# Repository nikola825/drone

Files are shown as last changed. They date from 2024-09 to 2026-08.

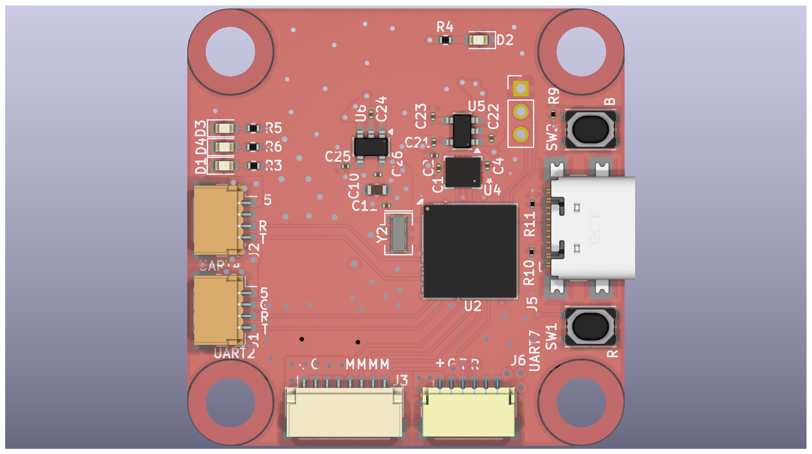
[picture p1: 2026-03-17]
hardware/fc/droneboardh723/render-top.png

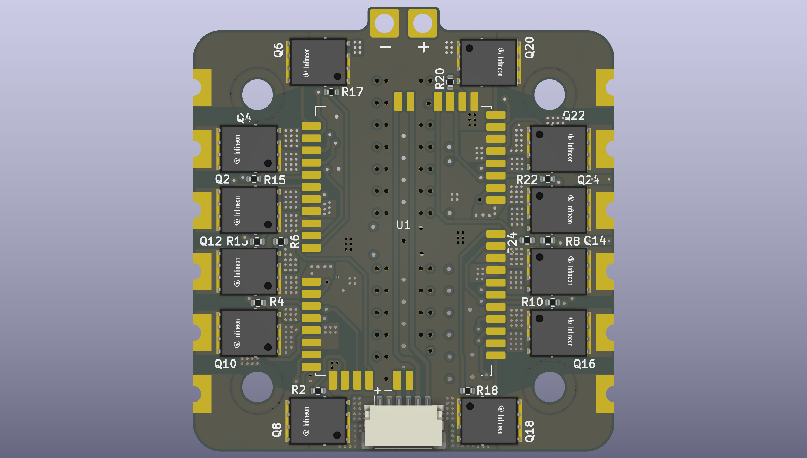
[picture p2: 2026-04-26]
hardware/esc/esc4x/power_board/top.png

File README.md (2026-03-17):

## 3D printable FPV quadcopter frame, SMT32-based flight controller and flight controller code

Hobby project, a homemade FPV drone with custom flight controller and frame.

### Current version - master branch
Folder contents (see readmes for more details):
- `3dp` - Freecad projects with 3D printable drone parts
- `code` - code for the flight controller
- `hardware` - KiCad projects for flight controller and esc PCB

Off the shelf parts you'll need:
- screws and screw related parts for the frame - see the readme in `3dp`
- motors and propellers
- ESC
- ELRS receiver
- Camera and VTX if you want FPV video

I couldn't be bothered to do in-detail docs, feel free to email me at (reverse the string to get my email) `moc.liamg@528alokin`

Do not use for anything serious, this was made by a man who started with zero knowledge of electronics, embedded development, rust development, flight controllers and 3D print design.
If you need something reliable, just get off-the-shelf stuff.

### Older versions
- `droneV1` branch contains the old Arduino-as-a-controller + MPU6050 version
- `droneV2` branch contains the old ATMEGA2560 flight controller board with an onboard MPU6050
- `droneV3` branch contains the work-in-progress version of the STM32F411 flight controller

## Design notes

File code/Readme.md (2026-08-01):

## Flight controller and configurator tool

This folder contains the flight_controller project to be flashed to the hardware in this repo.
It also contains the configurator GUI tool to configure motor mapping and directions of the flight controller.

### Contents
- `flight_controller` - Rust crate using the [Embassy](https://embassy.dev) implementing the flight control code
  - Cargo.toml contains feature flags for various variants of the FC PCB
  - Can be flashed through STM32 Cube programmer, dfu-util or probe-rs
- `configurator` - gui tool for configuring the motor mapping and directions
- `common` - stuff shared between configurator and FC
- `.vscode` and `.zed` - configurations for Rust analyzer for VSCode and Zed editors

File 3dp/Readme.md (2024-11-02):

## 3D printable 5-inch frame

- FcStd file contains the FreeCad project
- `complete.stl` - shows how the parts look assembled
- other STL files contain individual parts

Additional stuff needed for assembly:
- Screws - DIN 912 hex head screws of various lengths
  - M3x40 - 4 pieces
  - M3x12 - 8 pieces
  - M3x8 - 16 pieces
  - M3x20 - 4 pieces
- Heat set inserts M3, 4mm deep, 5mm wide - 8 pieces
- M3 5mm IN/OUT standoff - 8 pieces
- M3 30mm IN/IN standoffs - 8 pieces
- M3 washer - 8 pieces
- Silicone anti vibration mounts

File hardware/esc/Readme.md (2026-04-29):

# ESC

This folder contains PCBs for a 1x and a 4x ESC.
Mostly inspired by the [AM32 reference hardware](https://github.com/am32-firmware/am32-wiki/tree/ad24a0f2b645dd5e00588bb1a56035153b24e888/docs/development)

AM32REF_F051 target can be flashed using standard AM32 flashing process.

## esc1x
Contains one PCB for a single  ESC with solder points for power, control signal and ST-Link connections.

## esc4x 
Contains two PCBs - a logic board and a power board.

The boards are supposed to be soldered together using the castellated edges on the logic board and pads on the power board.

#### Logic board
This PCB contains the microcontrollers and gate drivers for the 4x esc.

It has no high power requirements. Can be fabricated as a cheaper 1 Oz/ft^2 thickness PCB

#### Power board
This PCB contains the mosfets, capacitors, regulators and connections for external stuff.

It is supposed to handle high currents of the motors and should be made with thicker 2 Oz/ft^2 copper.

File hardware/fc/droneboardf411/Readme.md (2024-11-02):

## Flight controller PCB
KiCad project and bom file for the flight controller PCB

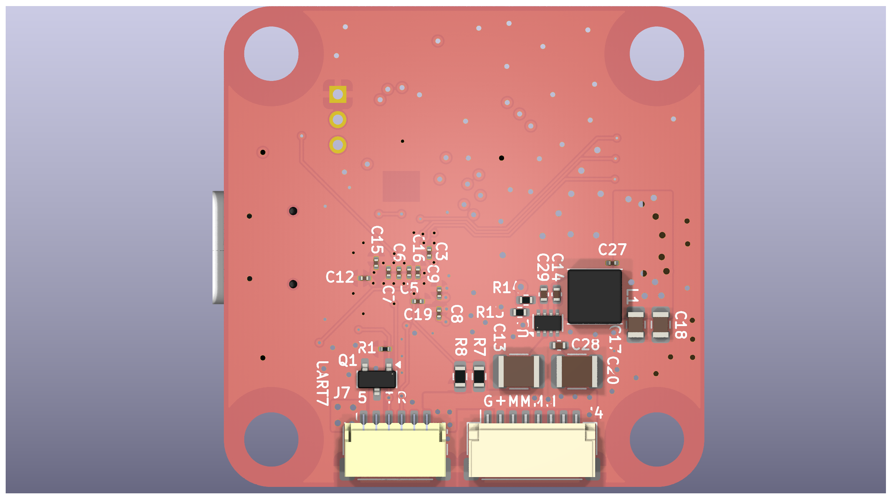
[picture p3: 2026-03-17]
hardware/fc/droneboardh723/render-bottom.png

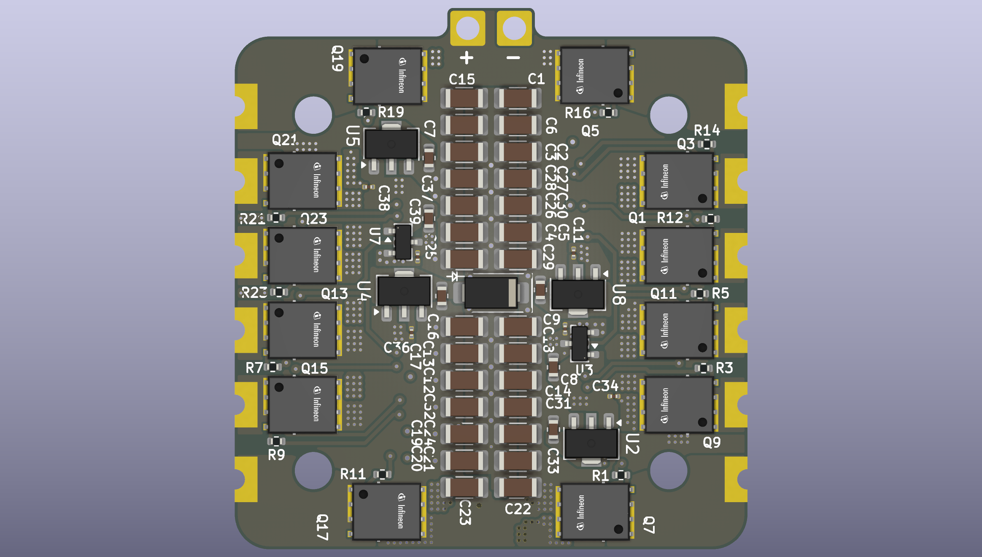
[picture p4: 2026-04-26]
hardware/esc/esc4x/power_board/bottom.png

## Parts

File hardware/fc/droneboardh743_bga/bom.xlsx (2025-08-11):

 |  |  | xxxx xxxx xxxxx xxPCS BOM (Sample Bill of Materials)
Item # | *Designator | *Qty | Manufacturer | *Mfg Part # | Description / Value | *Package/Footprint | Type | Your Instructions / Notes
1 | C3, C5, C6, C7, C8, C9, C16, C19, C27, C1 | 10 | Murata | GRM033R61A104KE15D | CAP CER 100nF 10V X5R 0201 | 0201 | SMD
2 | C12, C15, C2 | 3 | Murata | GRM033R61A225ME47D | CAP CER 2.2uF 10V X5R 0201 | 0201 | SMD
3 | C13, C20 | 2 | Samsung | CL32B106KBJNNNE | CAP CER 10uF 50V X7R 1210 | 1210 | SMD
4 | C14, C28 | 2 | Murata | GRM155R71H104KE14D | CAP CER 100nF 50V X7R 0402 | 0402 | SMD
5 | C17, C18 | 2 | Samsung | CL21A226MPQNNNE | CAP CER 22uF 10V X5R 0805 | 0805 | SMD
6 | C29 | 1 | Murata | GRM155R71H333KE14D | CAP CER 33nF 50V X7R 0402 | 0402 | SMD
7 | J4, J3 | 2 | JST | SM08B-SRSS-TB | JST SH Headers SMT SIDE 8-pin | JST SH 8-pin header | SMD
8 | J7, J6 | 2 | JST | SM06B-SRSS-TB | JST SH Headers SMT SIDE 6-pin | JST SH 6-pin header | SMD
9 | L1 | 1 | Coilcraft | XEL4030-332MEC | Power Inductors - SMD 3.3uH Shld 20% 6.6A 28.6mOhms AECQ2 | Inductor SMD 4x4mm | SMD
10 | Q1 | 1 | Diodes Incorporated | DMN3042L-7 | MOSFETs MOSFET N-CHANNEL 30V 5.8A SOT23-3 | SOT 23 | SMD
11 | R1, R9 | 2 | Yageo | RC0201FR-0710KL | RES 10K OHM 0.05W 1% 0201 | 0201 | SMD
12 | R7 | 1 | Yageo | RT0603BRD0710KL | RES 10K OHM 0.1W 0.1% 0603 | 0603 | SMD
13 | R8 | 1 | Yageo | RT0603BRD071KL | RES 1K OHM 0.1W 0.1% 0603 | 0603 | SMD
14 | R13, R3, R4, R5, R6 | 5 | Yageo | RC0402FR-071KL | RES 1K OHM 0.1W 1% 0402 | 0402 | SMD
15 | R14 | 1 | Yageo | RC0402FR-075K49L | RES 5.49K OHM 0.1W 1% 0402 | 0402 | SMD
16 | U1 | 1 | Texas Instruments | TPS62933FDRLR | Buck Switching Regulator IC Positive Adjustable 0.8V 1 Output 3A SOT-583 | SOT-583-8 | SMD
17 | C4, C23, C25 | 3 | Murata | GRM033R61C103KA12D | CAP CER 10nF 16V X5R 0201 | 0201 | SMD
18 | C10 | 1 | Samsung | CL10A106KP8NNNC | CAP CER 10uF 10V X5R 0603 | 0603 | SMD
19 | C11, C21, C22, C24, C26 | 5 | Murata | GRM033R61A105ME44D | CAP CER 1uF 10V X5R 0201 | 0201 | SMD
20 | D1 | 1 | Foshan NationStar | NCD0603Y5 | LED SMD Yellow 2V 20ma 0603 | 0603 | SMD
21 | D2 | 1 | Foshan NationStar | NCD0603R1 | LED SMD Red 2V 20ma 0603 | 0603 | SMD
22 | D3 | 1 | Foshan NationStar | NCD0603G3 | LED SMD Green 2V 20ma 0603 | 0603 | SMD
23 | D4 | 1 | Foshan NationStar | NCD0603B5 | LED SMD Blue 2V 20ma 0603 | 0603 | SMD
24 | J1, J2 | 2 | JST | SM04B-SRSS-TB | JST SH Headers SMT SIDE 4-pin | JST SH 4-pin header | SMD
25 | J5 | 1 | GCT | USB4110-GF-A | USB Connectors USB Type C, 2.0, Rec, SMT , G/F, RA , Top Mnt, T & R | USB-C | SMD
26 | R10, R11 | 2 | Yageo | RC0201FR-075K1L | RES 5.1K OHM 0.05W 1% 0201 | 0201 | SMD
27 | SW1, SW2 | 2 | Wurth Elektronik | 434133025816 | SWITCH TACTILE SPST-NO 0.05A 16V | Tactile switch 4.2x3.2mm | SMD
28 | U2 | 1 | STMicroelectronics | STM32H743VIH6 | ARM Microcontrollers - MCU High-performance, Arm Cortex-M7 MCU 2MBytes of Flash 1MB RAM | TFBGA-100 | SMD
29 | U4 | 1 | TDK Invensense | ICM-42688-P | IMUs - Inertial Measurement Units 6 Axis IMU Motion Tracking | LGA-14 3x2.5 P0.5 | SMD | Do not wash with ultrasound
30 | U5, U6 | 2 | MaxLinear | SPX3819M5-L-3-3/TR | LDO Voltage Regulators 500mA LOW NOISE LDO 3.3V | SOT-23-5 | SMD
31 | Y2 | 1 | Murata | CSTNE8M00G520000R0 | 8MHz 10pF SMD3213-3P Ceramic Resonators | 3-SMD, Non-Standard | SMD
Need a quick and accurante quote? Need an efficient production? Please read SMT Ordering Necessary Files & Info in 1 minute. Thank you very much! (https://www.pcbway.com/smt_ordering_guide.html)
Click for Instructions on How to Create a BOM (https://www.pcbway.com/blog/PCB_Assembly/How_to_Build_a_BOM__Bill_Of_Materials_.html)

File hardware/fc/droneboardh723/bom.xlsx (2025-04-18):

 |  |  | xxxx xxxx xxxxx xxPCS BOM (Sample Bill of Materials)
Item # | *Designator | *Qty | Manufacturer | *Mfg Part # | Description / Value | *Package/Footprint | Type | Your Instructions / Notes
1 | C13 | 1 | Don’t care | Don’t care | CAP CER 10uF 25V X7R 1210 | 1210 | SMD | Don’t care about model/manufacturer, just make sure it fits description
2 | C14 | 1 | Don’t care | Don’t care | CAP CER 100nF 25V X7R 0603 | 0603 | SMD | Don’t care about model/manufacturer, just make sure it fits description
3 | C17, C18 | 2 | Don’t care | Don’t care | CAP CER 22uF 10V X5R 0805 | 0805 | SMD | Don’t care about model/manufacturer, just make sure it fits description
4 | C1, C3, C5, C6, C7, C8, C9, C16 | 8 | Don’t care | Don’t care | CAP CER 100nF 16V X5R 0201 | 0201 | SMD | Don’t care about model/manufacturer, just make sure it fits description
5 | C2, C12, C15 | 3 | Don’t care | Don’t care | CAP CER 2.2uF 10V X5R 0201 | 0201 | SMD | Don’t care about model/manufacturer, just make sure it fits description
6 | C4, C23, C25 | 3 | Don’t care | Don’t care | CAP CER 10nF 16V X5R 0201 | 0201 | SMD | Don’t care about model/manufacturer, just make sure it fits description
7 | C10 | 1 | Don’t care | Don’t care | CAP CER 10uF 10V X5R 0402 | 0402 | SMD | Don’t care about model/manufacturer, just make sure it fits description
8 | C11, C21, C22, C24, C26 | 5 | Don’t care | Don’t care | CAP CER 1uF 10V X5R 0201 | 0201 | SMD
9 | D1 | 1 | Foshan NationStar | NCD0603Y5 | LED SMD Yellow 2V 20ma 0603 | 0603 | SMD
10 | D2 | 1 | Foshan NationStar | NCD0603R1 | LED SMD Red 2V 20ma 0603 | 0603 | SMD
11 | D3 | 1 | Foshan NationStar | NCD0603G3 | LED SMD Green 2V 20ma 0603 | 0603 | SMD
12 | D4 | 1 | Foshan NationStar | NCD0603B5 | LED SMD Blue 2V 20ma 0603 | 0603 | SMD
13 | J5 | 1 | GCT | USB4110-GF-A | USB Connectors USB Type C, 2.0, Rec, SMT , G/F, RA , Top Mnt, T & R | USB-C | SMD
14 | R1, R2, R9, R12 | 4 | Don’t care | Don’t care | RES 10K OHM 0.05W 1% 0201 | 0201 | SMD | Don’t care about model/manufacturer, just make sure it fits description
15 | R14 | 1 | Don’t care | Don’t care | RES 5.49K OHM 0.1W 1% 0402 | 0402 | SMD | Don’t care about model/manufacturer, just make sure it fits description
16 | R3, R4, R5, R6, R13 | 5 | Don’t care | Don’t care | RES 1K OHM 0.1W 1% 0402 | 0402 | SMD | Don’t care about model/manufacturer, just make sure it fits description
17 | R8 | 1 | Don’t care | Don’t care | RES 1K OHM 0.1W 0.1% 0603 | 0603 | SMD | Don’t care about model/manufacturer, just make sure it fits description
18 | R7 | 1 | Don’t care | Don’t care | RES 10K OHM 0.1W 0.1% 0603 | 0603 | SMD | Don’t care about model/manufacturer, just make sure it fits description
19 | R10, R11 | 2 | Don’t care | Don’t care | RES 5.1K OHM 0.05W 1% 0201 | 0201 | SMD | Don’t care about model/manufacturer, just make sure it fits description
20 | U1 | 1 | Diodes Incorporated | AP62300Z6-7 | Switching Voltage Regulators DCDC Conv HV Buck SOT563(STD) T&R 3K | SOT 563 | SMD
21 | U2 | 1 | STMicroelectronics | STM32H723VGT6 | ARM Microcontrollers High-performance, Arm Cortex-M7 MCU 1 MByte Flash, 564 Kbytes RAM | LQFP-100 | SMD
22 | U4 | 1 | TDK Invensense | ICM-42688-P | IMUs - Inertial Measurement Units 6 Axis IMU Motion Tracking | LGA-14 3x2.5 P0.5 | SMD | Do not wash with ultrasound
23 | U5, U6 | 2 | MaxLinear | SPX3819M5-L-3-3/TR | LDO Voltage Regulators 500mA LOW NOISE LDO 3.3V | SOT-23-5 | SMD
24 | Y2 | 1 | Murata Electronics | CSTNE20M0V53Z000R0 | Resonators 20.0 MHZ 15PF | 3-SMD, Non-Standard | SMD
25 | L1 | 1 | Coilcraft | XEL4030-332MEC | Power Inductors - SMD 3.3uH Shld 20% 6.6A 28.6mOhms AECQ2 | Inductor SMD 4x4mm | SMD
Need a quick and accurante quote? Need an efficient production? Please read SMT Ordering Necessary Files & Info in 1 minute. Thank you very much! (https://www.pcbway.com/smt_ordering_guide.html)
Click for Instructions on How to Create a BOM (https://www.pcbway.com/blog/PCB_Assembly/How_to_Build_a_BOM__Bill_Of_Materials_.html)

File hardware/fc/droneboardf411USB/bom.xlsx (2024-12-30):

 |  |  | xxxx xxxx xxxxx xxPCS BOM (Sample Bill of Materials)
Item # | *Designator | *Qty | Manufacturer | *Mfg Part # | Description / Value | *Package/Footprint | Type | Your Instructions / Notes
1 | C4, C23, C25 | 3 | Don’t care | Don’t care | CAP CER 10nF 16V X7R 0603 | 0603 | SMD | Don’t care about model/manufacturer, just make sure it fits description
2 | C1, C20 | 2 | Don’t care | Don’t care | CAP CER 100nF 16V X7R 0603 | 0603 | SMD | Don’t care about model/manufacturer, just make sure it fits description
3 | C3, C5, C6, C7, C9, C16 | 6 | Don’t care | Don’t care | CAP CER 100nF 16V X7R 0402 | 0402 | SMD | Don’t care about model/manufacturer, just make sure it fits description
4 | C19 | 1 | Don’t care | Don’t care | CAP CER 330nF 25V X7R 0805 | 0805 | SMD | Don’t care about model/manufacturer, just make sure it fits description
5 | C11, C21, C22, C24, C26 | 5 | Don’t care | Don’t care | CAP CER 1uF 16V X5R 0805 | 0805 | SMD | Don’t care about model/manufacturer, just make sure it fits description
6 | C2 | 1 | Don’t care | Don’t care | CAP CER 2.2uF 16V X7R 0805 | 0805 | SMD | Don’t care about model/manufacturer, just make sure it fits description
7 | C15 | 1 | Don’t care | Don’t care | CAP CER 4.7uF 16V X7R 1206 | 1206 | SMD | Don’t care about model/manufacturer, just make sure it fits description
8 | C10 | 1 | Don’t care | Don’t care | CAP CER 10uF 16V X7R 1206 | 1206 | SMD | Don’t care about model/manufacturer, just make sure it fits description
9 | D1 | 1 | Foshan NationStar | NCD0603Y5 | LED SMD Yellow 2V 20ma 0603 | 0603 | SMD
10 | D2 | 1 | Foshan NationStar | NCD0603R1 | LED SMD Red 2V 20ma 0603 | 0603 | SMD
11 | D3 | 1 | Foshan NationStar | NCD0603G3 | LED SMD Green 2V 20ma 0603 | 0603 | SMD
12 | D4 | 1 | Foshan NationStar | NCD0603B5 | LED SMD Blue 2V 20ma 0603 | 0603 | SMD
13 | R1,R2,R9 | 3 | Don’t care | Don’t care | RES 10K OHM 0.1W 1% 0402 SMD | 0402 | SMD | Don’t care about model/manufacturer, just make sure it fits description
14 | R7 | 1 | Don’t care | Don’t care | RES 10K OHM 0.1W 0.1% 0603 SMD | 0603 | SMD | Don’t care about model/manufacturer, just make sure it fits description
15 | R3, R4, R5, R6 | 4 | Don’t care | Don’t care | RES 1K OHM 0.1W 1% 0402 SMD | 0402 | SMD | Don’t care about model/manufacturer, just make sure it fits description
16 | R8 | 1 | Don’t care | Don’t care | RES 1K OHM 0.1W 0.1% 0603 SMD | 0603 | SMD | Don’t care about model/manufacturer, just make sure it fits description
17 | U1 | 1 | STMicroelectronics | STM32F411CEU6 | ARM Microcontrollers - MCU High-performance access line, Arm Cortex-M4 core DSP & FPU, 512 Kbytes of Flash | QFN-48 | SMD
18 | U3 | 1 | STMicroelectronics | L78M05CDT | Linear Voltage Regulators 5.0V 0.5A Positive | TO-252-2 | SMD
19 | U4 | 1 | TDK Invensense | ICM-42688-P | IMUs - Inertial Measurement Units 6 Axis IMU Motion Tracking | LGA-14 3x2.5 P0.5 | SMD
20 | U5,U6 | 2 | STMicroelectronics | LDK130M33R | LDO Voltage Regulators 300mA low Q LDO 1.9 to 5.5V 100mV | SOT-23-5 | SMD
21 | Y2 | 1 | Murata Electronics | CSTNE20M0V53Z000R0 | Resonators 20.0 MHZ 15PF | 3-SMD, Non-Standard | SMD
22 | J2 | 1 | Molex | 47346-0001 | USB Connectors MICRO USB B RECPT BTTM MOUNT | SMD | SMD
Need a quick and accurante quote? Need an efficient production? Please read SMT Ordering Necessary Files & Info in 1 minute. Thank you very much! (https://www.pcbway.com/smt_ordering_guide.html)
Click for Instructions on How to Create a BOM (https://www.pcbway.com/blog/PCB_Assembly/How_to_Build_a_BOM__Bill_Of_Materials_.html)

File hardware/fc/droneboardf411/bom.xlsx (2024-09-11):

 |  |  | xxxx xxxx xxxxx xxPCS BOM (Sample Bill of Materials)
Item # | *Designator | *Qty | Manufacturer | *Mfg Part # | Description / Value | *Package/Footprint | Type | Your Instructions / Notes
1 | C4, C23, C25 | 3 | Don’t care | Don’t care | CAP CER 10nF 16V X7R 0603 | 0603 | SMD | Don’t care about model/manufacturer, just make sure it fits description
2 | C1, C20 | 2 | Don’t care | Don’t care | CAP CER 100nF 16V X7R 0603 | 0603 | SMD | Don’t care about model/manufacturer, just make sure it fits description
3 | C3, C5, C6, C7, C9, C16 | 6 | Don’t care | Don’t care | CAP CER 100nF 16V X7R 0402 | 0402 | SMD | Don’t care about model/manufacturer, just make sure it fits description
4 | C19 | 1 | Don’t care | Don’t care | CAP CER 330nF 25V X7R 0805 | 0805 | SMD | Don’t care about model/manufacturer, just make sure it fits description
5 | C11, C21, C22, C24, C26 | 5 | Don’t care | Don’t care | CAP CER 1uF 16V X5R 0805 | 0805 | SMD | Don’t care about model/manufacturer, just make sure it fits description
6 | C2 | 1 | Don’t care | Don’t care | CAP CER 2.2uF 16V X7R 0805 | 0805 | SMD | Don’t care about model/manufacturer, just make sure it fits description
 | C15 | 1 | Don’t care | Don’t care | CAP CER 4.7uF 16V X7R 1206 | 1206 | SMD | Don’t care about model/manufacturer, just make sure it fits description
 | C10 | 1 | Don’t care | Don’t care | CAP CER 10uF 16V X7R 1206 | 1206 | SMD | Don’t care about model/manufacturer, just make sure it fits description
 | D1 | 1 | Don’t care | Don’t care | LED SMD Yellow 2V 20ma 0603 | 0603 | SMD | Don’t care about model/manufacturer, just make sure it fits description
 | D2 | 1 | Don’t care | Don’t care | LED SMD Red 2V 20ma 0603 | 0603 | SMD | Don’t care about model/manufacturer, just make sure it fits description
 | D3 | 1 | Don’t care | Don’t care | LED SMD Green 2V 20ma 0603 | 0603 | SMD | Don’t care about model/manufacturer, just make sure it fits description
 | D4 | 1 | Don’t care | Don’t care | LED SMD Blue 2V 20ma 0603 | 0603 | SMD | Don’t care about model/manufacturer, just make sure it fits description
 | R1,R2,R9 | 3 | Don’t care | Don’t care | RES 10K OHM 0.1W 1% 0402 SMD | 0402 | SMD | Don’t care about model/manufacturer, just make sure it fits description
 | R7 | 1 | Don’t care | Don’t care | RES 10K OHM 0.1W 1% 0603 SMD | 0603 | SMD | Don’t care about model/manufacturer, just make sure it fits description
 | R3, R4, R5, R6 | 4 | Don’t care | Don’t care | RES 1K OHM 0.1W 1% 0402 SMD | 0402 | SMD | Don’t care about model/manufacturer, just make sure it fits description
 | R8 | 1 | Don’t care | Don’t care | RES 1K OHM 0.1W 1% 0603 SMD | 0603 | SMD | Don’t care about model/manufacturer, just make sure it fits description
 | U1 | 1 | STMicroelectronics | STM32F411CEU6 | ARM Microcontrollers - MCU High-performance access line, Arm Cortex-M4 core DSP & FPU, 512 Kbytes of Flash | QFN-48 | SMD
 | U3 | 1 | STMicroelectronics | L78M05CDT | Linear Voltage Regulators 5.0V 0.5A Positive | TO-252-2 | SMD
 | U4 | 1 | TDK Invensense | ICM-42688-P | IMUs - Inertial Measurement Units 6 Axis IMU Motion Tracking | LGA-14 3x2.5 P0.5 | SMD
 | U5,U6 | 2 | STMicroelectronics | LDK130M33R | LDO Voltage Regulators 300mA low Q LDO 1.9 to 5.5V 100mV | SOT-23-5 | SMD
 | Y2 | 1 | Murata Electronics | CSTNE20M0V53Z000R0 | Resonators 20.0 MHZ 15PF | 3-SMD, Non-Standard | SMD
Need a quick and accurante quote? Need an efficient production? Please read SMT Ordering Necessary Files & Info in 1 minute. Thank you very much! (https://www.pcbway.com/smt_ordering_guide.html)
Click for Instructions on How to Create a BOM (https://www.pcbway.com/blog/PCB_Assembly/How_to_Build_a_BOM__Bill_Of_Materials_.html)

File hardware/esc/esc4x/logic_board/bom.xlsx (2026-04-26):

 |  |  | xxxx xxxx xxxxx xxPCS BOM (Sample Bill of Materials)
Item # | *Designator | *Qty | Manufacturer | *Mfg Part # | Description / Value | *Package/Footprint | Type | Your Instructions / Notes
1 | R5,R39,R8,R3,R23,R18,R24,R37,R42,R27,R11,R26,R36,R20,R15,R9,R30,R13,R16,R6,R1,R44,R40,R34,R29,R22,R32,R12 | 28 | Yageo | RC0201FR-0710KL | RES 10K OHM 0.05W 1% 0201 | 0201 | SMD
2 | R38,R31,R41,R17,R14,R4,R7,R10,R2,R21,R25,R43,R28,R35,R33,R19 | 16 | Yageo | RC0201FR-071KL | RES 1K OHM 0.05W 1% 0201 | 0201 | SMD
3 | U3,U1,U7,U5 | 4 | STMicroelectronics | STM32F051K8U6TR | ARM Microcontrollers - MCU ARM Cortex-M0 MCU 64Kb Flash 48MHz | UFQFPN-32 | SMD
4 | C23,C5,C33,C9,C10,C18,C27,C32,C22,C31,C42,C43,C38,C11,C24,C44 | 16 | Murata | GRM033R61A105ME44D | CAP CER 1uF 10V X5R 0201 | 0201 | SMD
5 | C21,C2,C12,C3,C8,C35,C36,C1,C30,C14,C13,C17,C25,C15,C34,C41 | 16 | Murata | GRM033R61A104KE15D | CAP CER 100nF 10V X5R 0201 | 0201 | SMD
6 | C4,C7,C26,C40,C29,C37,C20,C16 | 8 | Samsung | CL05A106MP5NUNC | CAP CER 10uF 10V X5R 0402 | 0402 | SMD
7 | C19,C6,C39,C28 | 4 | Murata | GRM033R61C103KA12D | CAP CER 10nF 16V X5R 0201 | 0201 | SMD
8 | U6,U8,U2,U4 | 4 | Texas instruments | DRV8300DRGER | Gate Drivers 100-V max simple 3-p hase gate driver | VQFN-24 | SMD
Need a quick and accurante quote? Need an efficient production? Please read SMT Ordering Necessary Files & Info in 1 minute. Thank you very much! (https://www.pcbway.com/smt_ordering_guide.html)
Click for Instructions on How to Create a BOM (https://www.pcbway.com/blog/PCB_Assembly/How_to_Build_a_BOM__Bill_Of_Materials_.html)

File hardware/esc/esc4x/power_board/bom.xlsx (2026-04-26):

 |  |  | xxxx xxxx xxxxx xxPCS BOM (Sample Bill of Materials)
Item # | *Designator | *Qty | Manufacturer | *Mfg Part # | Description / Value | *Package/Footprint | Type | Your Instructions / Notes
1 | C1, C2, C3, C4, C5, C6, C7, C12, C13, C14, C15, C16, C17, C18, C19, C20, C21, C22, C23, C24, C25, C26, C27, C28, C29, C30, C31, C32 | 28 | TDK | C3216X5R1E476M160AC | CAP CER 47uF 25V X5R 1206 | 1206 | SMD
2 | C8, C10, C33, C35, C37, C39 | 6 | Murata | GCJ188R71E105KA01D | CAP CER 1uF 25V X7R 0603 | 0603 | SMD
3 | C9, C11, C34, C36, C38, C40 | 6 | Murata | GRM033R61A105ME44D | CAP CER 1uF 10V X5R 0201 | 0201 | SMD
4 | D3 | 1 | Yageo | SMAJ26A-HP6AT | VS Diodes SMAJ DO214AC 26V 42.1V AEC-Q101 | DO-214AC | SMD
5 | J1 | 1 | JST | SM06B-SRSS-TB | JST SH Headers SMT SIDE 6-pin | JST SH 6-pin header | SMD
6 | Q1, Q2, Q3, Q4, Q5, Q6, Q7, Q8, Q9, Q10, Q11, Q12, Q13, Q14, Q15, Q16, Q17, Q18, Q19, Q20, Q21, Q22, Q23, Q24 | 24 | Infineon | BSC010N04LS6 | N-Channel 40 V 100A 3W Surface Mount PG-TDSON-8-6 | TDSON-8-FL | SMD
7 | R1, R2, R3, R4, R5, R6, R7, R8, R9, R10, R11, R12, R13, R14, R15, R16, R17, R18, R19, R20, R21, R22, R23, R24 | 24 | Yageo | RC0402FR-0720RL | RES 20 OHM 0.067W 1% 0402 | 0402 | SMD
8 | U2, U4, U5, U8 | 4 | Diodes incorporated | AP7381-50Y-13 | LDO Voltage Regulators 150mA 5V | SOT-89-3 | SMD
9 | U3, U7 | 2 | Diodes incorporated | AP7381-33SA-7 | LDO Voltage Regulator 100mA 3.3V | SOT-23-3 | SMD
Need a quick and accurante quote? Need an efficient production? Please read SMT Ordering Necessary Files & Info in 1 minute. Thank you very much! (https://www.pcbway.com/smt_ordering_guide.html)
Click for Instructions on How to Create a BOM (https://www.pcbway.com/blog/PCB_Assembly/How_to_Build_a_BOM__Bill_Of_Materials_.html)

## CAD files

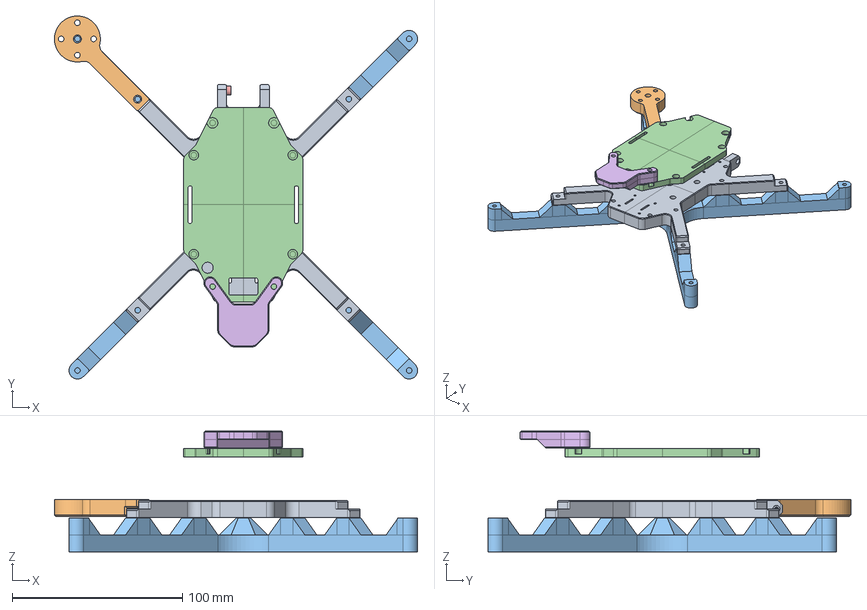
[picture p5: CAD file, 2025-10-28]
3dp/seven_inch/whole_assembly.step
213.1 x 213.0 x 70.9 mm
Center
Arm
Legs
Top
CameraAttachment
GPSPlate

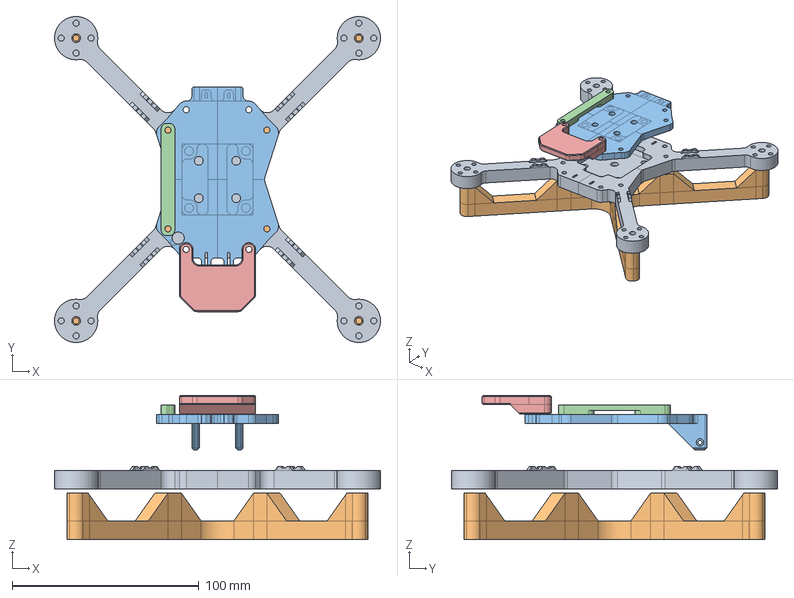
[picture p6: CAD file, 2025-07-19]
3dp/five_inch/whole_assembly.step
174.5 x 174.5 x 77.3 mm
Bottom
Legs
Top
TiePoint
GPSPlate

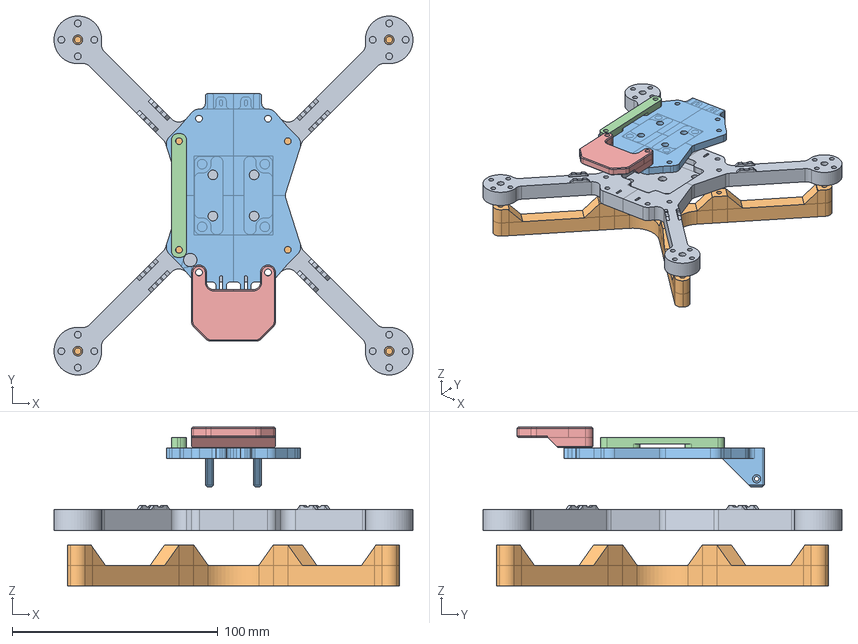
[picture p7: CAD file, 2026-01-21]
3dp/five_inch/five_inch.FCStd
174.5 x 174.5 x 77.3 mm
Bottom
Legs
Top
TiePoint
GPSPlate

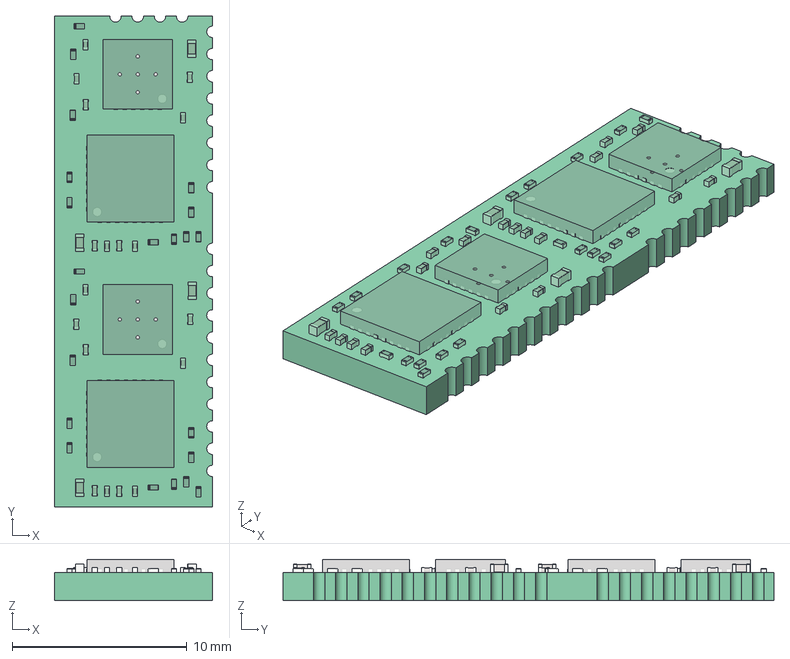
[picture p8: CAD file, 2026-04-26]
hardware/esc/esc4x/logic_board/logic_board1-logic_board.step
9.04 x 28.1 x 2.37 mm
Pcb_7dd1
R5_R_0201_0603Metric_fb9afff6527c x 22
U3_QFN-32-1EP_5x5mm_Pitch0.5mm_a1086153c562 x 2
C23_C_0201_0603Metric_5a5157595c69 x 18
C4_C_0402_1005Metric_eb0286e01f0b x 4
U2_QFN-24-1EP_4x4mm_Pitch0.5mm_a600a1f0b4fe[2] x 2

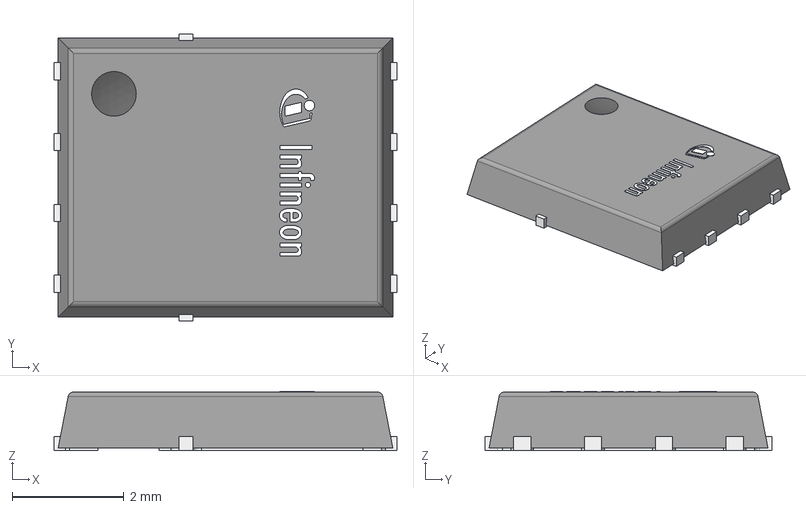
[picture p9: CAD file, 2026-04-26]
hardware/esc/esc4x/power_board/components/3dmodels/PG_TDSON_FL.stp
6.15 x 5.15 x 1.06 mm

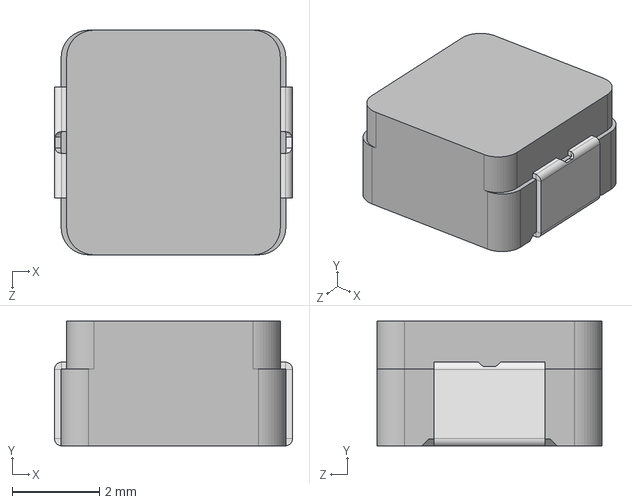
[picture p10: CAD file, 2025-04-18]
hardware/fc/droneboardh723/components/3dmodels/IHLP2020CZ.STEP
5.45 x 2.86 x 5.15 mm

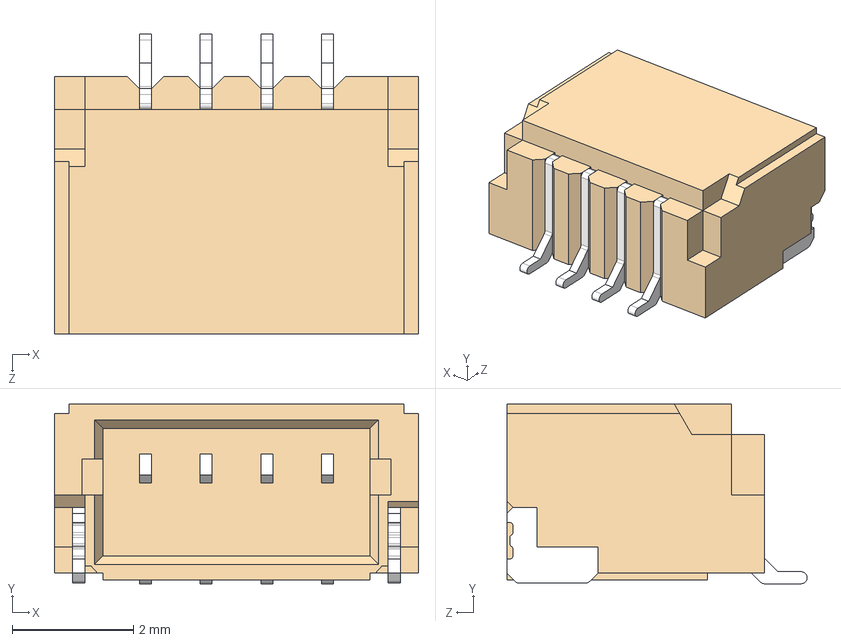
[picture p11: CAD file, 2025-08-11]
hardware/fc/droneboardh743_bga/components/3dmodels/SM04B-SRSS-TB_LF__SN_.stp
6.00 x 2.96 x 4.95 mm

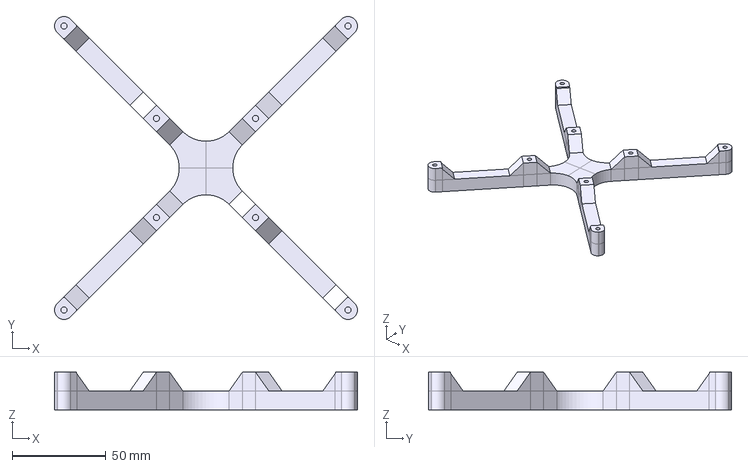
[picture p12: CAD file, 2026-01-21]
3dp/five_inch/legs.step
161.4 x 161.4 x 20.0 mm

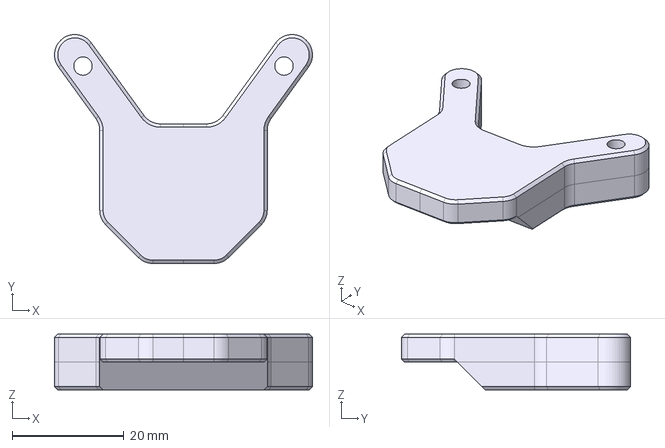
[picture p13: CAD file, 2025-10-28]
3dp/seven_inch/gps_plate.step
46.2 x 41.0 x 10.0 mm

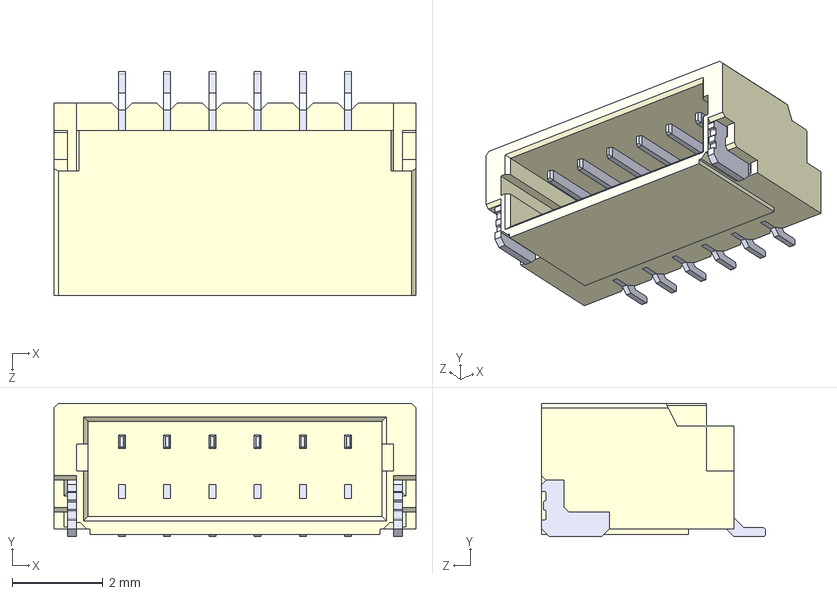
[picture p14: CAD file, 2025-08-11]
hardware/esc/esc4x/power_board/components/3dmodels/SM06B-SRSS-TB--3DModel-STEP-269445.STEP
8.00 x 2.95 x 4.95 mm

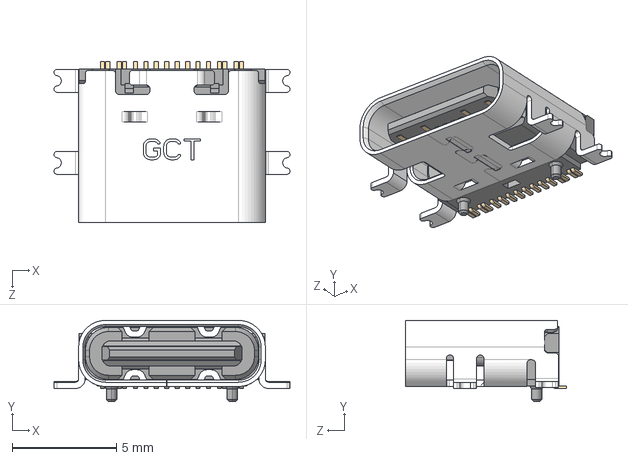
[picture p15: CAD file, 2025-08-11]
hardware/fc/droneboardh743_bga/components/3dmodels/USB4110GFA--3DModel-STEP-269445.STEP
11.3 x 3.89 x 7.70 mm

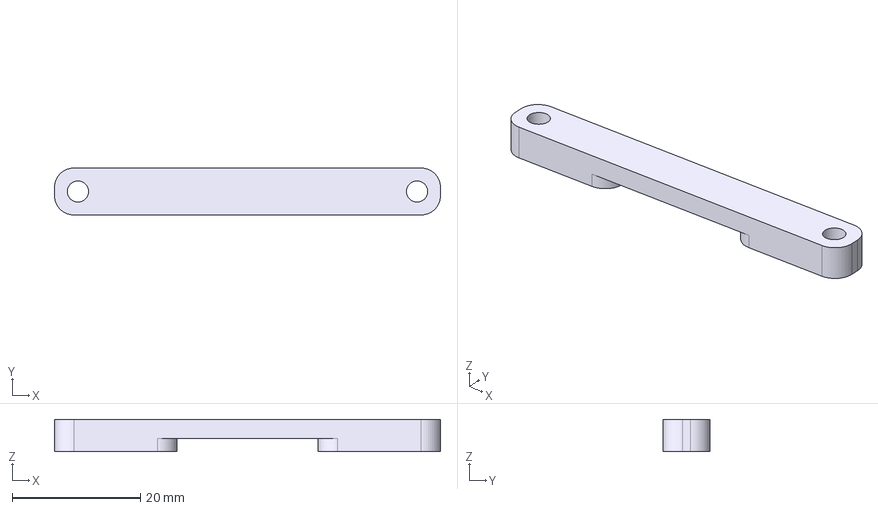
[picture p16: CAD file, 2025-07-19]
3dp/five_inch/tie_point.step
60.1 x 7.30 x 5.00 mm

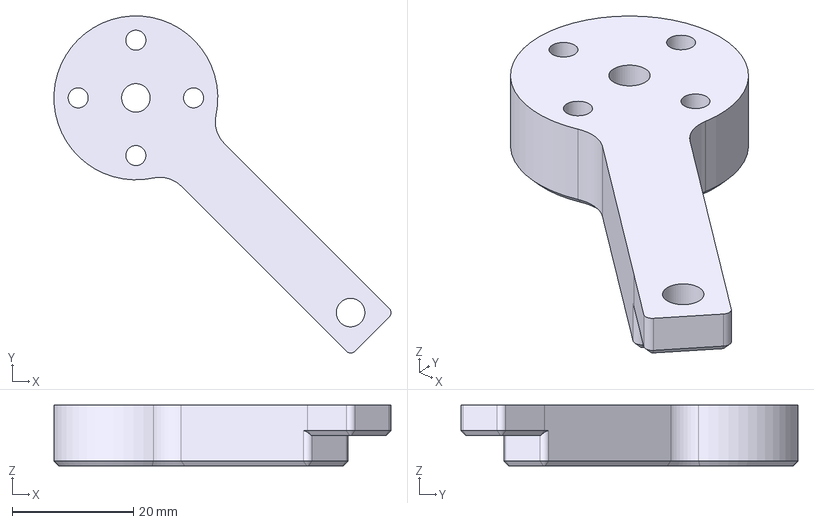
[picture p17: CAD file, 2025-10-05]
3dp/seven_inch/arm.step
55.5 x 55.5 x 10.0 mm

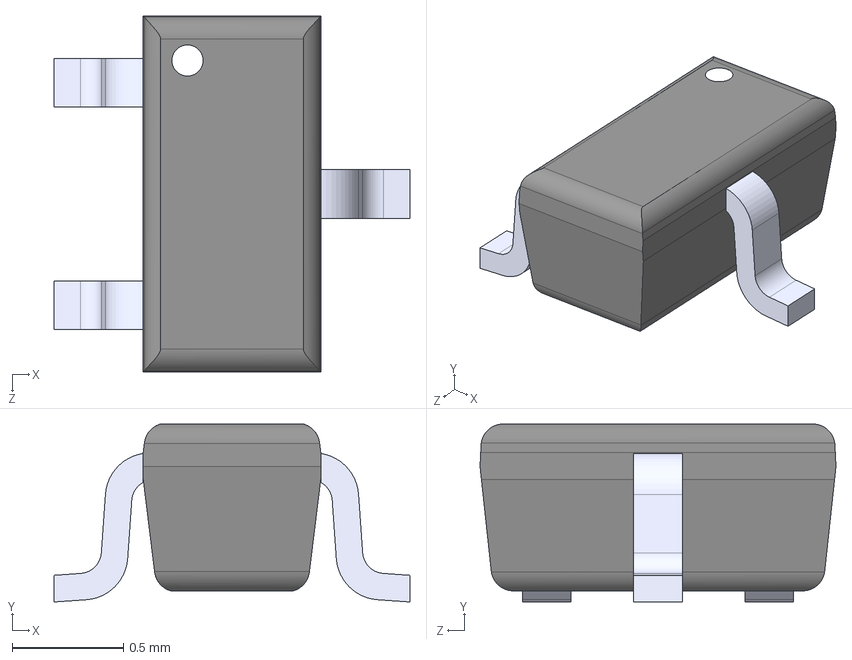
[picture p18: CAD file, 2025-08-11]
hardware/fc/droneboardh743_bga/components/3dmodels/SOT-523.STEP
1.60 x 0.8 x 1.60 mm

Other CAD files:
hardware/esc/esc4x/logic_board/logic_board.step
3dp/seven_inch/seven_inch.FCStd
3dp/five_inch/gps_plate.step
3dp/seven_inch/center.step
3dp/five_inch/bottom.step
3dp/five_inch/bottom.stl
3dp/five_inch/gps_plate.stl
3dp/five_inch/legs.stl
3dp/five_inch/tie_point.stl
3dp/five_inch/top.step
3dp/five_inch/top.stl
3dp/seven_inch/arm.stl
3dp/seven_inch/center.stl
3dp/seven_inch/gps_plate.stl
3dp/seven_inch/legs.step
3dp/seven_inch/legs.stl
3dp/seven_inch/top.step
3dp/seven_inch/top.stl
3dp/seven_inch/whole_assembly.stl
hardware/fc/droneboardh743_bga/components/3dmodels/434133025816.stp
hardware/fc/droneboardh743_bga/components/3dmodels/KMR221GLFS--3DModel-STEP-56544.STEP
hardware/fc/droneboardh743_bga/components/3dmodels/SM08B-SRSS-TB (LF)(SN)--3DModel-STEP-269445.STEP

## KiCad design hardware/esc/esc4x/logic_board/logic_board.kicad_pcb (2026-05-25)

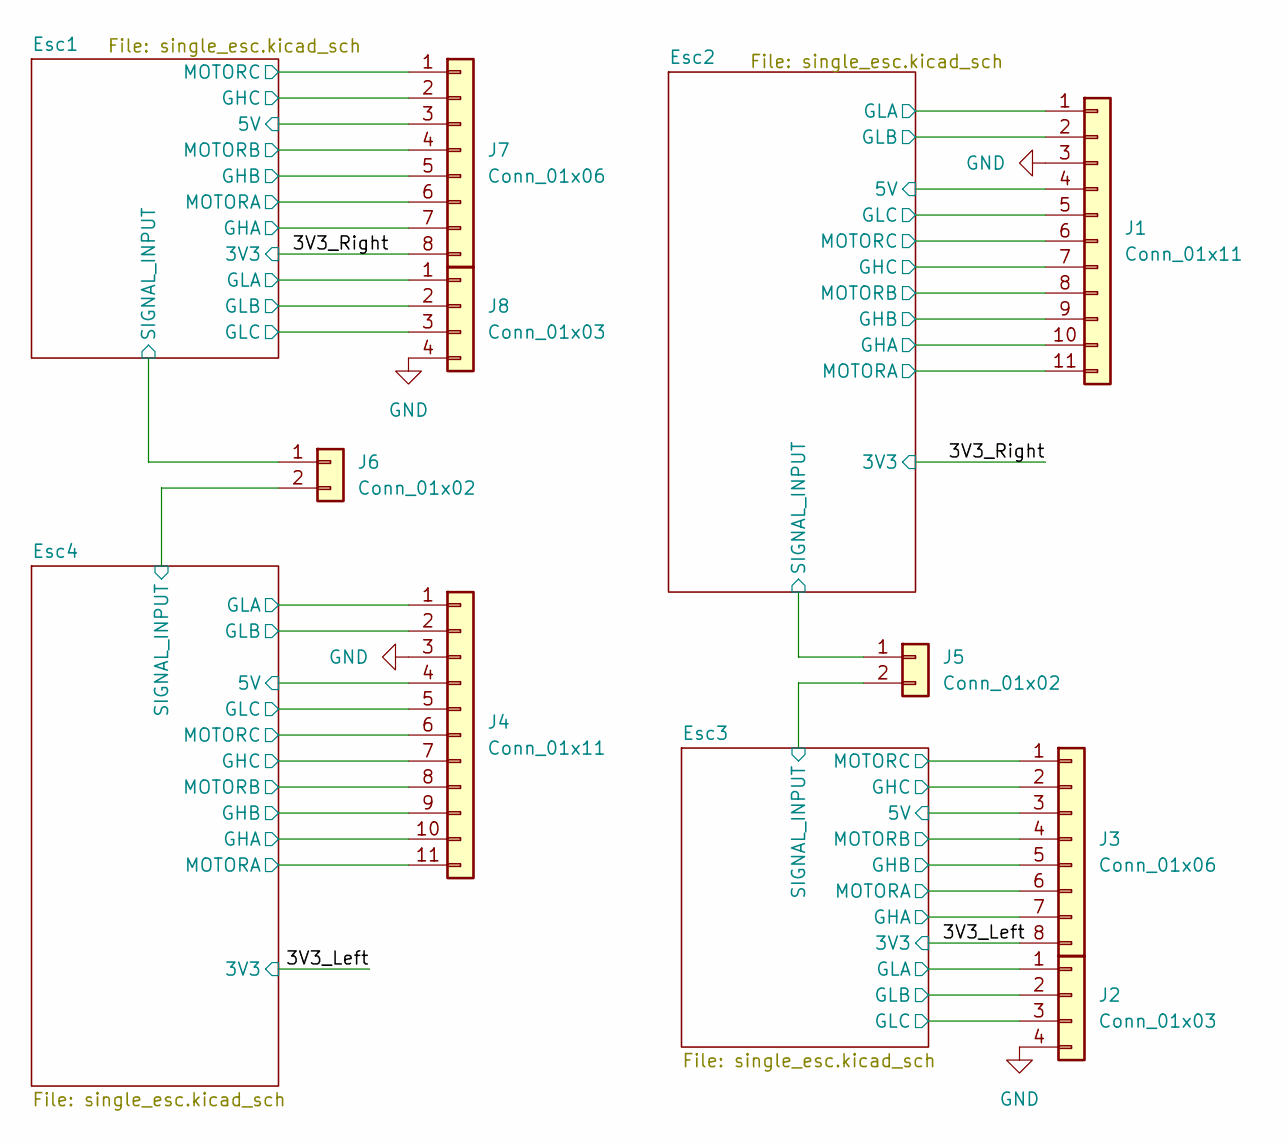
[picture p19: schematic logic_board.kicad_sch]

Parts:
J1, J4: Conn_01x11; Castellated11Pin127
J2, J8: Conn_01x03; Castellated4Pin127
J3, J7: Conn_01x06; Castellated8Pin127
J5, J6: Conn_01x02; Castellated2Pin127

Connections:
/3V3_Left: J3.8; also elsewhere on the board
/3V3_Right: J7.8; also elsewhere on the board
/Esc1/5V: J7.3; also elsewhere on the board
/Esc1/GHA: J7.7; also elsewhere on the board
/Esc1/GHB: J7.5; also elsewhere on the board
/Esc1/GHC: J7.2; also elsewhere on the board
/Esc1/GLA: J8.1; also elsewhere on the board
/Esc1/GLB: J8.2; also elsewhere on the board
/Esc1/GLC: J8.3; also elsewhere on the board
/Esc1/MOTORA: J7.6; also elsewhere on the board
/Esc1/MOTORB: J7.4; also elsewhere on the board
/Esc1/MOTORC: J7.1; also elsewhere on the board
/Esc1/SIGNAL_INPUT: J6.1; also elsewhere on the board
/Esc2/5V: J1.4; also elsewhere on the board
/Esc2/GHA: J1.10; also elsewhere on the board
/Esc2/GHB: J1.9; also elsewhere on the board
/Esc2/GHC: J1.7; also elsewhere on the board
/Esc2/GLA: J1.1; also elsewhere on the board
/Esc2/GLB: J1.2; also elsewhere on the board
/Esc2/GLC: J1.5; also elsewhere on the board
/Esc2/MOTORA: J1.11; also elsewhere on the board
/Esc2/MOTORB: J1.8; also elsewhere on the board
/Esc2/MOTORC: J1.6; also elsewhere on the board
/Esc2/SIGNAL_INPUT: J5.1; also elsewhere on the board
/Esc3/5V: J3.3; also elsewhere on the board
/Esc3/GHA: J3.7; also elsewhere on the board
/Esc3/GHB: J3.5; also elsewhere on the board
/Esc3/GHC: J3.2; also elsewhere on the board
/Esc3/GLA: J2.1; also elsewhere on the board
/Esc3/GLB: J2.2; also elsewhere on the board
/Esc3/GLC: J2.3; also elsewhere on the board
/Esc3/MOTORA: J3.6; also elsewhere on the board
/Esc3/MOTORB: J3.4; also elsewhere on the board
/Esc3/MOTORC: J3.1; also elsewhere on the board
/Esc3/SIGNAL_INPUT: J5.2; also elsewhere on the board
/Esc4/5V: J4.4; also elsewhere on the board
/Esc4/GHA: J4.10; also elsewhere on the board
/Esc4/GHB: J4.9; also elsewhere on the board
/Esc4/GHC: J4.7; also elsewhere on the board
/Esc4/GLA: J4.1; also elsewhere on the board
/Esc4/GLB: J4.2; also elsewhere on the board
/Esc4/GLC: J4.5; also elsewhere on the board
/Esc4/MOTORA: J4.11; also elsewhere on the board
/Esc4/MOTORB: J4.8; also elsewhere on the board
/Esc4/MOTORC: J4.6; also elsewhere on the board
/Esc4/SIGNAL_INPUT: J6.2; also elsewhere on the board
GND: J1.3, J2.4, J4.3, J8.4; also elsewhere on the board

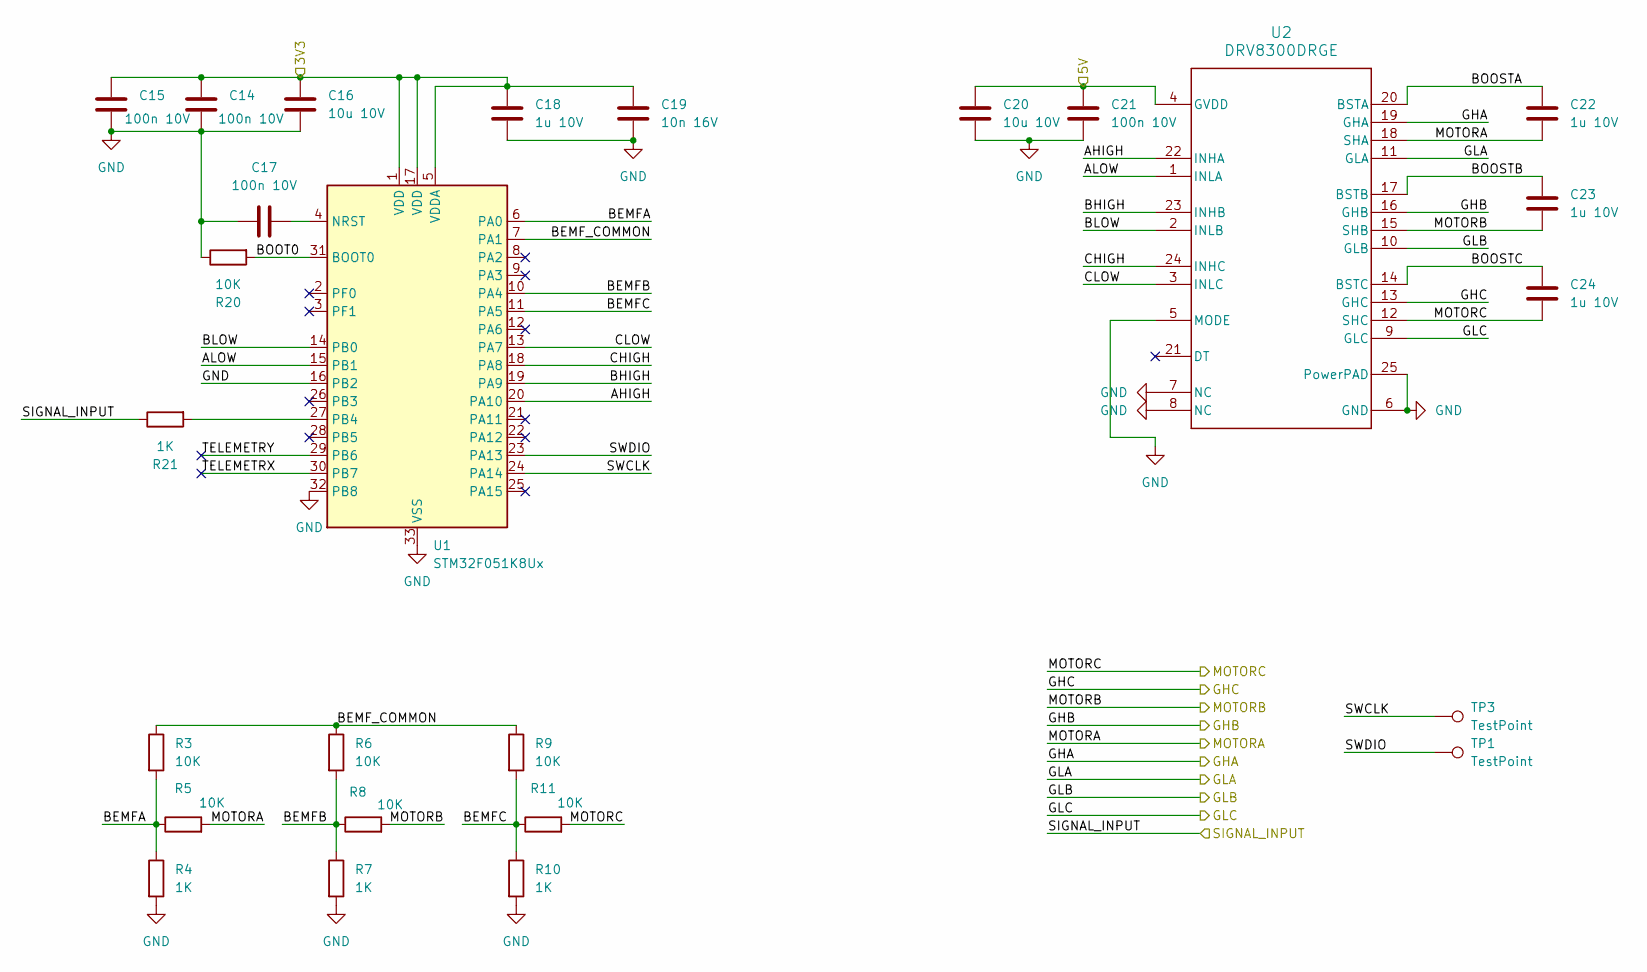
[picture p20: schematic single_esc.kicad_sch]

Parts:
C14, C15, C17, C21: 100n 10V; C_0201_0603Metric
C16, C20: 10u 10V; C_0402_1005Metric
C18, C22, C23, C24: 1u 10V; C_0201_0603Metric
C19: 10n 16V; C_0201_0603Metric
R3, R5, R6, R8, R9, R11, R20: 10K; R_0201_0603Metric
R4, R7, R10, R21: 1K; R_0201_0603Metric
TP1, TP3: TestPoint; SW_Testpoint
U1: STM32F051K8Ux; QFN-32-1EP_5x5mm_P0.5mm_EP3.45x3.45mm-Custom
U2: DRV8300DRGE; VQFN-24-1EP_4x4mm_P0.5mm_EP2.45x2.45mm_ThermalVias-Custom

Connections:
/3V3_Right: C14.2, C15.2, C16.2, C18.1, C19.2, U1.1 (VDD), U1.5 (VDDA), U1.17 (VDD); also elsewhere on the board
/Esc1/5V: C20.2, C21.2, U2.4 (GVDD); also elsewhere on the board
/Esc1/AHIGH: U1.20 (PA10), U2.22 (INHA)
/Esc1/ALOW: U1.15 (PB1), U2.1 (INLA)
/Esc1/BEMFA: R3.2, R4.1, R5.1, U1.6 (PA0)
/Esc1/BEMFB: R6.2, R7.1, R8.1, U1.10 (PA4)
/Esc1/BEMFC: R9.2, R10.1, R11.1, U1.11 (PA5)
/Esc1/BEMF_COMMON: R3.1, R6.1, R9.1, U1.7 (PA1)
/Esc1/BHIGH: U1.19 (PA9), U2.23 (INHB)
/Esc1/BLOW: U1.14 (PB0), U2.2 (INLB)
/Esc1/BOOSTA: C22.2, U2.20 (BSTA)
/Esc1/BOOSTB: C23.2, U2.17 (BSTB)
/Esc1/BOOSTC: C24.2, U2.14 (BSTC)
/Esc1/BOOT0: R20.2, U1.31 (BOOT0)
/Esc1/CHIGH: U1.18 (PA8), U2.24 (INHC)
/Esc1/CLOW: U1.13 (PA7), U2.3 (INLC)
/Esc1/GHA: U2.19 (GHA); also elsewhere on the board
/Esc1/GHB: U2.16 (GHB); also elsewhere on the board
/Esc1/GHC: U2.13 (GHC); also elsewhere on the board
/Esc1/GLA: U2.11 (GLA); also elsewhere on the board
/Esc1/GLB: U2.10 (GLB); also elsewhere on the board
/Esc1/GLC: U2.9 (GLC); also elsewhere on the board
/Esc1/MOTORA: C22.1, R5.2, U2.18 (SHA); also elsewhere on the board
/Esc1/MOTORB: C23.1, R8.2, U2.15 (SHB); also elsewhere on the board
/Esc1/MOTORC: C24.1, R11.2, U2.12 (SHC); also elsewhere on the board
/Esc1/SIGNAL_INPUT: R21.1; also elsewhere on the board
/Esc1/SWCLK: TP3.1, U1.24 (PA14)
/Esc1/SWDIO: TP1.1, U1.23 (PA13)
/Esc1/TELEMETRX: U1.30 (PB7)
/Esc1/TELEMETRY: U1.29 (PB6)
GND: C14.1, C15.1, C16.1, C17.2, C18.2, C19.1, C20.1, C21.1, R4.2, R7.2, R10.2, R20.1, U1.16 (PB2), U1.32 (PB8), U1.33 (VSS), U2.5 (MODE), U2.6 (GND), U2.7 (NC), U2.8 (NC), U2.25 (PowerPAD); also elsewhere on the board
unnamed: C17.1, U1.4 (NRST)
unnamed: R21.2, U1.27 (PB4)

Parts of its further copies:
C1, C2, C3, C8, C12, C13, C25, C30, C34, C35, C36, C41: 100n 10V; C_0201_0603Metric
C4, C7, C26, C29, C37, C40: 10u 10V; C_0402_1005Metric
C5, C9, C10, C11, C27, C31, C32, C33, C38, C42, C43, C44: 1u 10V; C_0201_0603Metric
C6, C28, C39: 10n 16V; C_0201_0603Metric
R1, R12, R13, R15, R16, R18, R22, R23, R24, R26, R27, R29, R30, R32, R34, R36, R37, R39, R40, R42, R44: 10K; R_0201_0603Metric
R2, R14, R17, R19, R25, R28, R31, R33, R35, R38, R41, R43: 1K; R_0201_0603Metric
TP2, TP4, TP5, TP6, TP7, TP8: TestPoint; SW_Testpoint
U3, U5, U7: STM32F051K8Ux; QFN-32-1EP_5x5mm_P0.5mm_EP3.45x3.45mm-Custom
U4, U6, U8: DRV8300DRGE; VQFN-24-1EP_4x4mm_P0.5mm_EP2.45x2.45mm_ThermalVias-Custom

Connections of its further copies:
/3V3_Left: C12.2, C13.2, C26.2, C27.1, C28.2, C34.2, C35.2, C37.2, C38.1, C39.2, U5.1 (VDD), U5.5 (VDDA), U5.17 (VDD), U7.1 (VDD), U7.5 (VDDA), U7.17 (VDD); also elsewhere on the board
/3V3_Right: C1.2, C2.2, C4.2, C5.1, C6.2, U3.1 (VDD), U3.5 (VDDA), U3.17 (VDD); also elsewhere on the board
/Esc2/5V: C7.2, C8.2, U4.4 (GVDD); also elsewhere on the board
/Esc2/AHIGH: U3.20 (PA10), U4.22 (INHA)
/Esc2/ALOW: U3.15 (PB1), U4.1 (INLA)
/Esc2/BEMFA: R1.2, R2.1, R12.1, U3.6 (PA0)
/Esc2/BEMFB: R13.2, R14.1, R15.1, U3.10 (PA4)
/Esc2/BEMFC: R16.2, R17.1, R18.1, U3.11 (PA5)
/Esc2/BEMF_COMMON: R1.1, R13.1, R16.1, U3.7 (PA1)
/Esc2/BHIGH: U3.19 (PA9), U4.23 (INHB)
/Esc2/BLOW: U3.14 (PB0), U4.2 (INLB)
/Esc2/BOOSTA: C9.2, U4.20 (BSTA)
/Esc2/BOOSTB: C10.2, U4.17 (BSTB)
/Esc2/BOOSTC: C11.2, U4.14 (BSTC)
/Esc2/BOOT0: R22.2, U3.31 (BOOT0)
/Esc2/CHIGH: U3.18 (PA8), U4.24 (INHC)
/Esc2/CLOW: U3.13 (PA7), U4.3 (INLC)
/Esc2/GHA: U4.19 (GHA); also elsewhere on the board
/Esc2/GHB: U4.16 (GHB); also elsewhere on the board
/Esc2/GHC: U4.13 (GHC); also elsewhere on the board
/Esc2/GLA: U4.11 (GLA); also elsewhere on the board
/Esc2/GLB: U4.10 (GLB); also elsewhere on the board
/Esc2/GLC: U4.9 (GLC); also elsewhere on the board
/Esc2/MOTORA: C9.1, R12.2, U4.18 (SHA); also elsewhere on the board
/Esc2/MOTORB: C10.1, R15.2, U4.15 (SHB); also elsewhere on the board
/Esc2/MOTORC: C11.1, R18.2, U4.12 (SHC); also elsewhere on the board
/Esc2/SIGNAL_INPUT: R19.1; also elsewhere on the board
/Esc2/SWCLK: TP2.1, U3.24 (PA14)
/Esc2/SWDIO: TP4.1, U3.23 (PA13)
/Esc2/TELEMETRX: U3.30 (PB7)
/Esc2/TELEMETRY: U3.29 (PB6)
/Esc3/5V: C29.2, C30.2, U6.4 (GVDD); also elsewhere on the board
/Esc3/AHIGH: U5.20 (PA10), U6.22 (INHA)
/Esc3/ALOW: U5.15 (PB1), U6.1 (INLA)
/Esc3/BEMFA: R24.2, R25.1, R26.1, U5.6 (PA0)
/Esc3/BEMFB: R27.2, R28.1, R29.1, U5.10 (PA4)
/Esc3/BEMFC: R30.2, R31.1, R32.1, U5.11 (PA5)
/Esc3/BEMF_COMMON: R24.1, R27.1, R30.1, U5.7 (PA1)
/Esc3/BHIGH: U5.19 (PA9), U6.23 (INHB)
/Esc3/BLOW: U5.14 (PB0), U6.2 (INLB)
/Esc3/BOOSTA: C31.2, U6.20 (BSTA)
/Esc3/BOOSTB: C32.2, U6.17 (BSTB)
/Esc3/BOOSTC: C33.2, U6.14 (BSTC)
/Esc3/BOOT0: R34.2, U5.31 (BOOT0)
/Esc3/CHIGH: U5.18 (PA8), U6.24 (INHC)
/Esc3/CLOW: U5.13 (PA7), U6.3 (INLC)
/Esc3/GHA: U6.19 (GHA); also elsewhere on the board
/Esc3/GHB: U6.16 (GHB); also elsewhere on the board
/Esc3/GHC: U6.13 (GHC); also elsewhere on the board
/Esc3/GLA: U6.11 (GLA); also elsewhere on the board
/Esc3/GLB: U6.10 (GLB); also elsewhere on the board
/Esc3/GLC: U6.9 (GLC); also elsewhere on the board
/Esc3/MOTORA: C31.1, R26.2, U6.18 (SHA); also elsewhere on the board
/Esc3/MOTORB: C32.1, R29.2, U6.15 (SHB); also elsewhere on the board
/Esc3/MOTORC: C33.1, R32.2, U6.12 (SHC); also elsewhere on the board
/Esc3/SIGNAL_INPUT: R33.1; also elsewhere on the board
/Esc3/SWCLK: TP5.1, U5.24 (PA14)
/Esc3/SWDIO: TP6.1, U5.23 (PA13)
/Esc3/TELEMETRX: U5.30 (PB7)
/Esc3/TELEMETRY: U5.29 (PB6)
/Esc4/5V: C40.2, C41.2, U8.4 (GVDD); also elsewhere on the board
/Esc4/AHIGH: U7.20 (PA10), U8.22 (INHA)
/Esc4/ALOW: U7.15 (PB1), U8.1 (INLA)
/Esc4/BEMFA: R23.2, R35.1, R36.1, U7.6 (PA0)
/Esc4/BEMFB: R37.2, R38.1, R39.1, U7.10 (PA4)
/Esc4/BEMFC: R40.2, R41.1, R42.1, U7.11 (PA5)
/Esc4/BEMF_COMMON: R23.1, R37.1, R40.1, U7.7 (PA1)
/Esc4/BHIGH: U7.19 (PA9), U8.23 (INHB)
/Esc4/BLOW: U7.14 (PB0), U8.2 (INLB)
/Esc4/BOOSTA: C42.2, U8.20 (BSTA)
/Esc4/BOOSTB: C43.2, U8.17 (BSTB)
/Esc4/BOOSTC: C44.2, U8.14 (BSTC)
/Esc4/BOOT0: R44.2, U7.31 (BOOT0)
/Esc4/CHIGH: U7.18 (PA8), U8.24 (INHC)
/Esc4/CLOW: U7.13 (PA7), U8.3 (INLC)
/Esc4/GHA: U8.19 (GHA); also elsewhere on the board
/Esc4/GHB: U8.16 (GHB); also elsewhere on the board
/Esc4/GHC: U8.13 (GHC); also elsewhere on the board
/Esc4/GLA: U8.11 (GLA); also elsewhere on the board
/Esc4/GLB: U8.10 (GLB); also elsewhere on the board
/Esc4/GLC: U8.9 (GLC); also elsewhere on the board
/Esc4/MOTORA: C42.1, R36.2, U8.18 (SHA); also elsewhere on the board
/Esc4/MOTORB: C43.1, R39.2, U8.15 (SHB); also elsewhere on the board
/Esc4/MOTORC: C44.1, R42.2, U8.12 (SHC); also elsewhere on the board
/Esc4/SIGNAL_INPUT: R43.1; also elsewhere on the board
/Esc4/SWCLK: TP7.1, U7.24 (PA14)
/Esc4/SWDIO: TP8.1, U7.23 (PA13)
/Esc4/TELEMETRX: U7.30 (PB7)
/Esc4/TELEMETRY: U7.29 (PB6)
GND: C1.1, C2.1, C3.2, C4.1, C5.2, C6.1, C7.1, C8.1, C12.1, C13.1, C25.2, C26.1, C27.2, C28.1, C29.1, C30.1, C34.1, C35.1, C36.2, C37.1, C38.2, C39.1, C40.1, C41.1, R2.2, R14.2, R17.2, R22.1, R25.2, R28.2, R31.2, R34.1, R35.2, R38.2, R41.2, R44.1, U3.16 (PB2), U3.32 (PB8), U3.33 (VSS), U4.5 (MODE), U4.6 (GND), U4.7 (NC), U4.8 (NC), U4.25 (PowerPAD), U5.16 (PB2), U5.32 (PB8), U5.33 (VSS), U6.5 (MODE), U6.6 (GND), U6.7 (NC), U6.8 (NC), U6.25 (PowerPAD), U7.16 (PB2), U7.32 (PB8), U7.33 (VSS), U8.5 (MODE), U8.6 (GND), U8.7 (NC), U8.8 (NC), U8.25 (PowerPAD); also elsewhere on the board
unnamed: C3.1, U3.4 (NRST)
unnamed: R19.2, U3.27 (PB4)
unnamed: C25.1, U5.4 (NRST)
unnamed: R33.2, U5.27 (PB4)
unnamed: C36.1, U7.4 (NRST)
unnamed: R43.2, U7.27 (PB4)

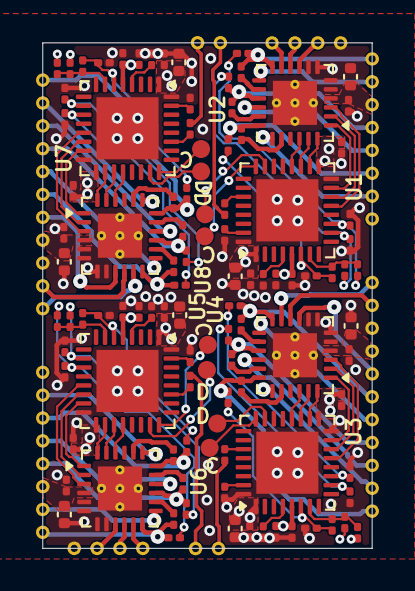
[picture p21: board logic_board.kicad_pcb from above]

Board: 4 copper layers, 18.3 x 28.1 mm, 112 parts (0 on the bottom side), 119 nets.

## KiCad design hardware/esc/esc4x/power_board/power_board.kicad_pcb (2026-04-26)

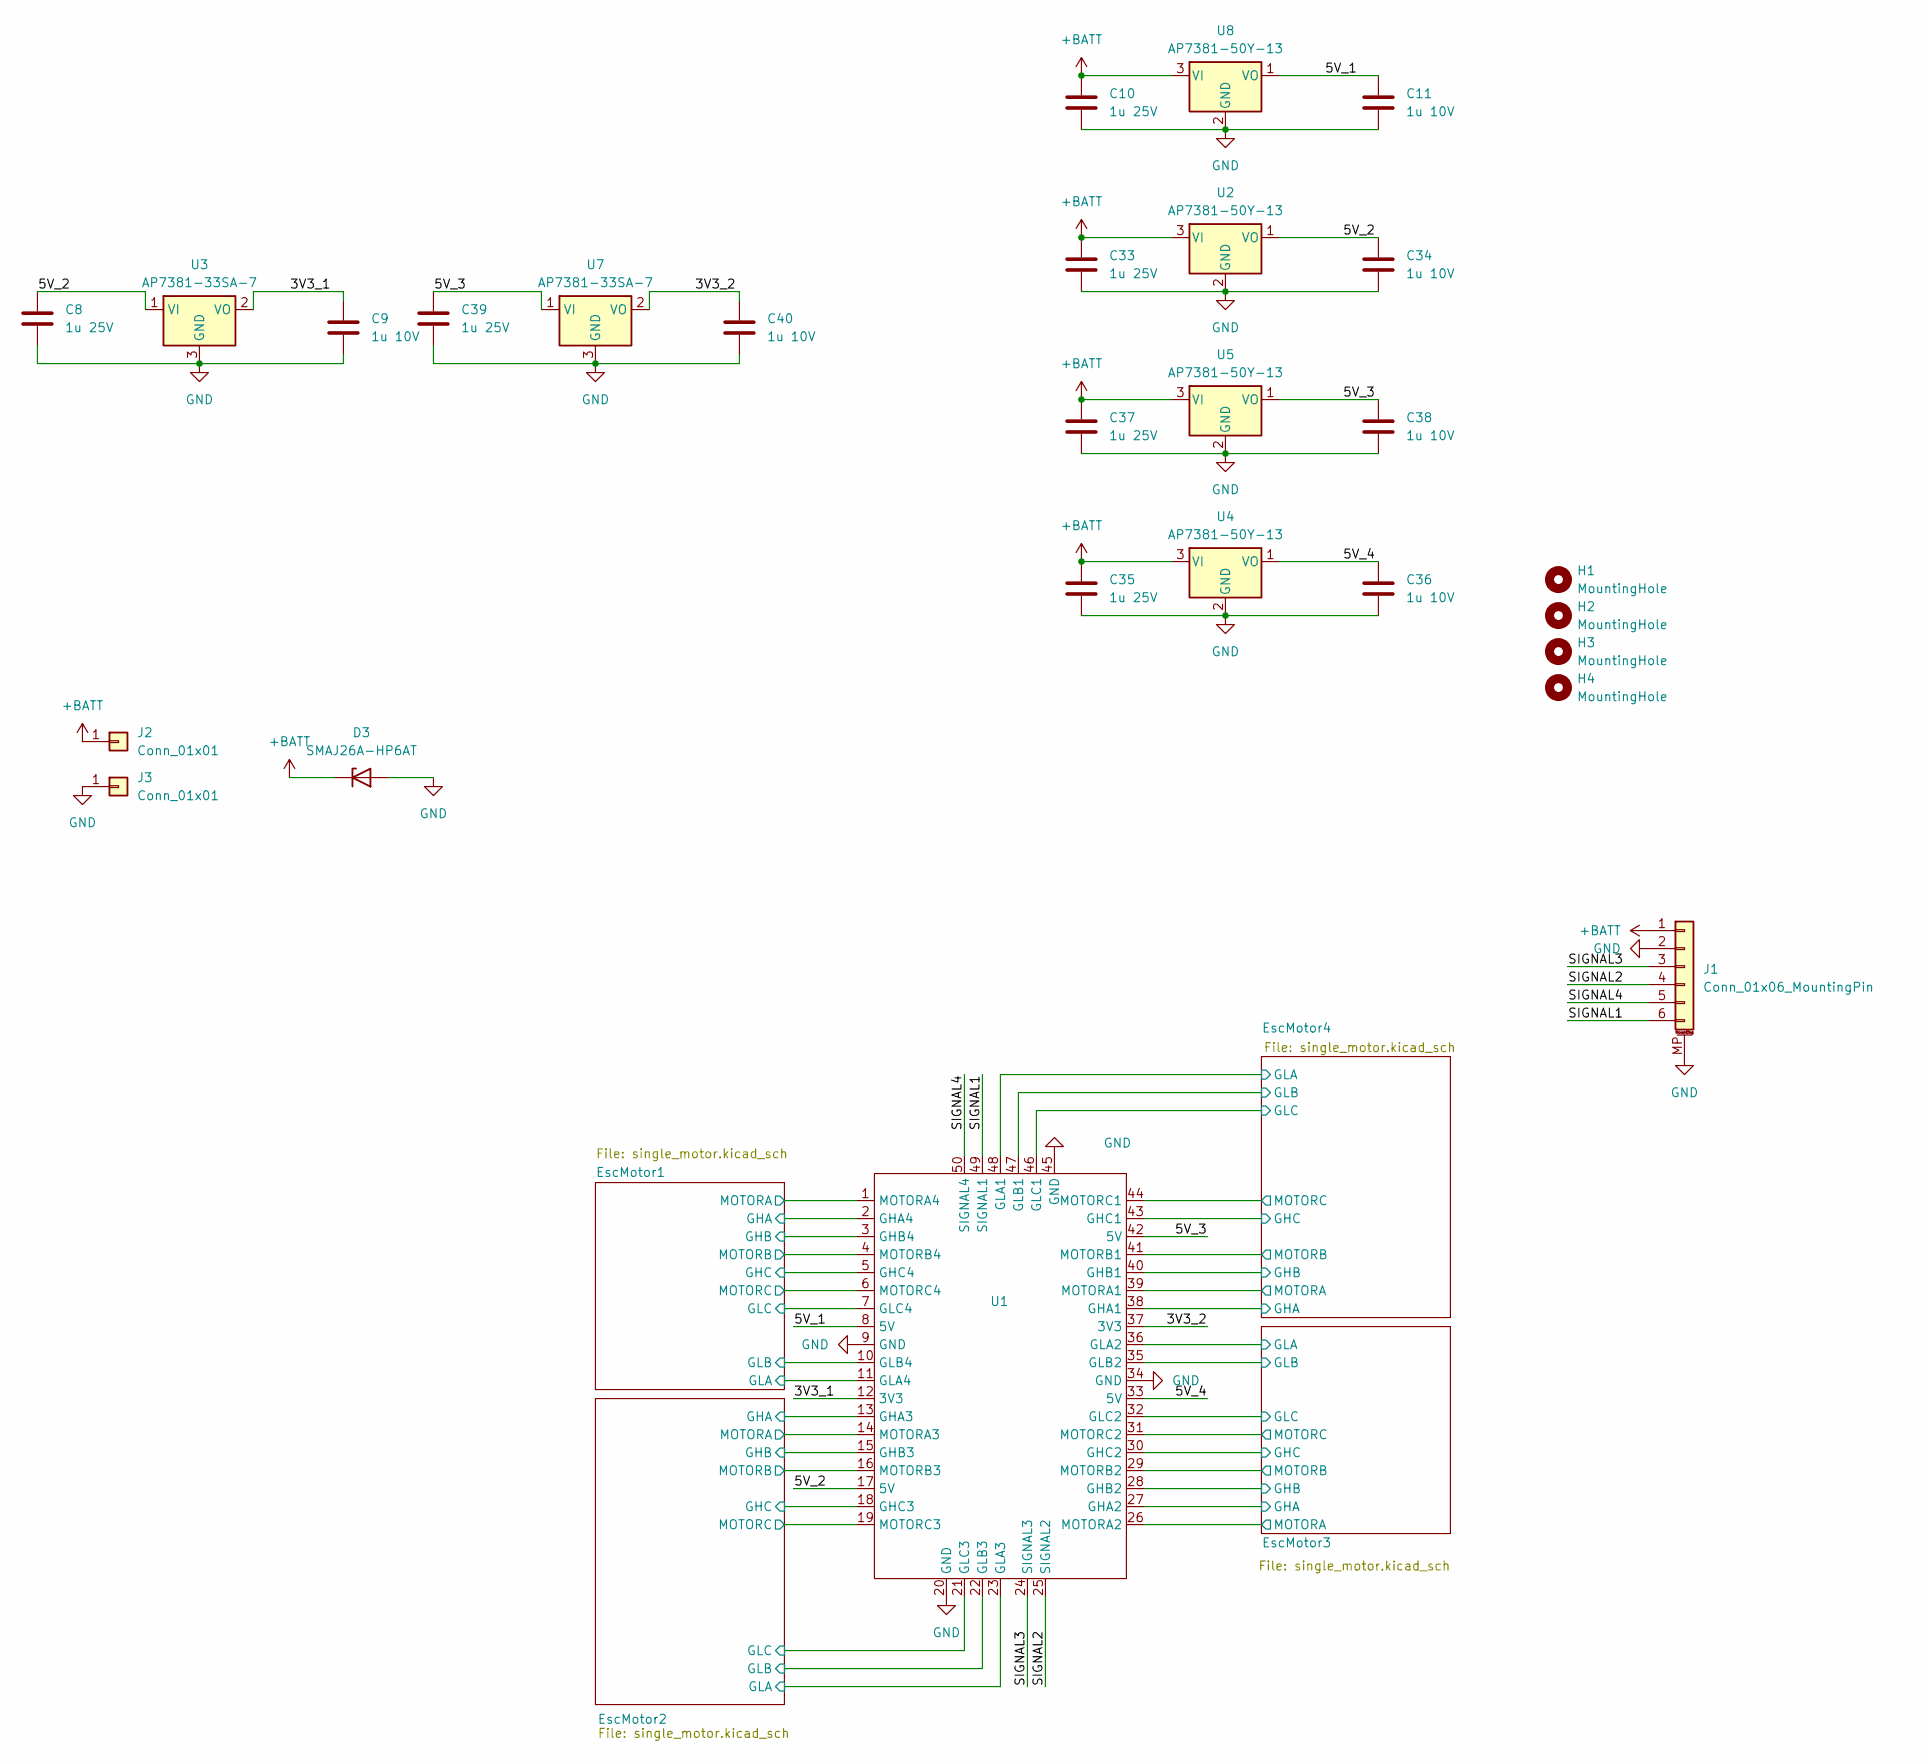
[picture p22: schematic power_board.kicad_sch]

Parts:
C8, C10, C33, C35, C37, C39: 1u 25V; C_0603_1608Metric
C9, C11, C34, C36, C38, C40: 1u 10V; C_0201_0603Metric
D3: SMAJ26A-HP6AT; D_SMA
H1, H2, H3, H4: MountingHole; EscScrewHole
J1: Conn_01x06_MountingPin; JST_SH_SM06B-SRSS-TB_1x06-1MP_P1.00mm_Horizontal
J2, J3: Conn_01x01; EscBatteryConnector
U1: LogicBoard
U2, U4, U5, U8: AP7381-50Y-13; SOT-89-3
U3, U7: AP7381-33SA-7; SOT-23

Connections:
+BATT: C10.1, C33.1, C35.1, C37.1, D3.1 (K), J1.1, J2.1 (Pin_1_1), U2.3 (VI), U4.3 (VI), U5.3 (VI), U8.3 (VI); also elsewhere on the board
/3V3_1: C9.1, U1.12 (3V3), U3.2 (VO)
/3V3_2: C40.1, U1.37 (3V3), U7.2 (VO)
/5V_1: C11.1, U1.8 (5V), U8.1 (VO)
/5V_2: C8.1, C34.1, U1.17 (5V), U2.1 (VO), U3.1 (VI)
/5V_3: C38.1, C39.1, U1.42 (5V), U5.1 (VO), U7.1 (VI)
/5V_4: C36.1, U1.33 (5V), U4.1 (VO)
/EscMotor1/GHA: U1.2 (GHA4); also elsewhere on the board
/EscMotor1/GHB: U1.3 (GHB4); also elsewhere on the board
/EscMotor1/GHC: U1.5 (GHC4); also elsewhere on the board
/EscMotor1/GLA: U1.11 (GLA4); also elsewhere on the board
/EscMotor1/GLB: U1.10 (GLB4); also elsewhere on the board
/EscMotor1/GLC: U1.7 (GLC4); also elsewhere on the board
/EscMotor1/MOTORA: U1.1 (MOTORA4); also elsewhere on the board
/EscMotor1/MOTORB: U1.4 (MOTORB4); also elsewhere on the board
/EscMotor1/MOTORC: U1.6 (MOTORC4); also elsewhere on the board
/EscMotor2/GHA: U1.13 (GHA3); also elsewhere on the board
/EscMotor2/GHB: U1.15 (GHB3); also elsewhere on the board
/EscMotor2/GHC: U1.18 (GHC3); also elsewhere on the board
/EscMotor2/GLA: U1.23 (GLA3); also elsewhere on the board
/EscMotor2/GLB: U1.22 (GLB3); also elsewhere on the board
/EscMotor2/GLC: U1.21 (GLC3); also elsewhere on the board
/EscMotor2/MOTORA: U1.14 (MOTORA3); also elsewhere on the board
/EscMotor2/MOTORB: U1.16 (MOTORB3); also elsewhere on the board
/EscMotor2/MOTORC: U1.19 (MOTORC3); also elsewhere on the board
/EscMotor3/GHA: U1.27 (GHA2); also elsewhere on the board
/EscMotor3/GHB: U1.28 (GHB2); also elsewhere on the board
/EscMotor3/GHC: U1.30 (GHC2); also elsewhere on the board
/EscMotor3/GLA: U1.36 (GLA2); also elsewhere on the board
/EscMotor3/GLB: U1.35 (GLB2); also elsewhere on the board
/EscMotor3/GLC: U1.32 (GLC2); also elsewhere on the board
/EscMotor3/MOTORA: U1.26 (MOTORA2); also elsewhere on the board
/EscMotor3/MOTORB: U1.29 (MOTORB2); also elsewhere on the board
/EscMotor3/MOTORC: U1.31 (MOTORC2); also elsewhere on the board
/EscMotor4/GHA: U1.38 (GHA1); also elsewhere on the board
/EscMotor4/GHB: U1.40 (GHB1); also elsewhere on the board
/EscMotor4/GHC: U1.43 (GHC1); also elsewhere on the board
/EscMotor4/GLA: U1.48 (GLA1); also elsewhere on the board
/EscMotor4/GLB: U1.47 (GLB1); also elsewhere on the board
/EscMotor4/GLC: U1.46 (GLC1); also elsewhere on the board
/EscMotor4/MOTORA: U1.39 (MOTORA1); also elsewhere on the board
/EscMotor4/MOTORB: U1.41 (MOTORB1); also elsewhere on the board
/EscMotor4/MOTORC: U1.44 (MOTORC1); also elsewhere on the board
/SIGNAL1: J1.6, U1.49 (SIGNAL1)
/SIGNAL2: J1.4, U1.25 (SIGNAL2)
/SIGNAL3: J1.3, U1.24 (SIGNAL3)
/SIGNAL4: J1.5, U1.50 (SIGNAL4)
GND: C8.2, C9.2, C10.2, C11.2, C33.2, C34.2, C35.2, C36.2, C37.2, C38.2, C39.2, C40.2, D3.2 (A), J1.2, J1.MP (MountPin), J3.1 (Pin_1_1), U1.9 (GND), U1.20 (GND), U1.34 (GND), U1.45 (GND), U2.2 (GND), U3.3 (GND), U4.2 (GND), U5.2 (GND), U7.3 (GND), U8.2 (GND); also elsewhere on the board

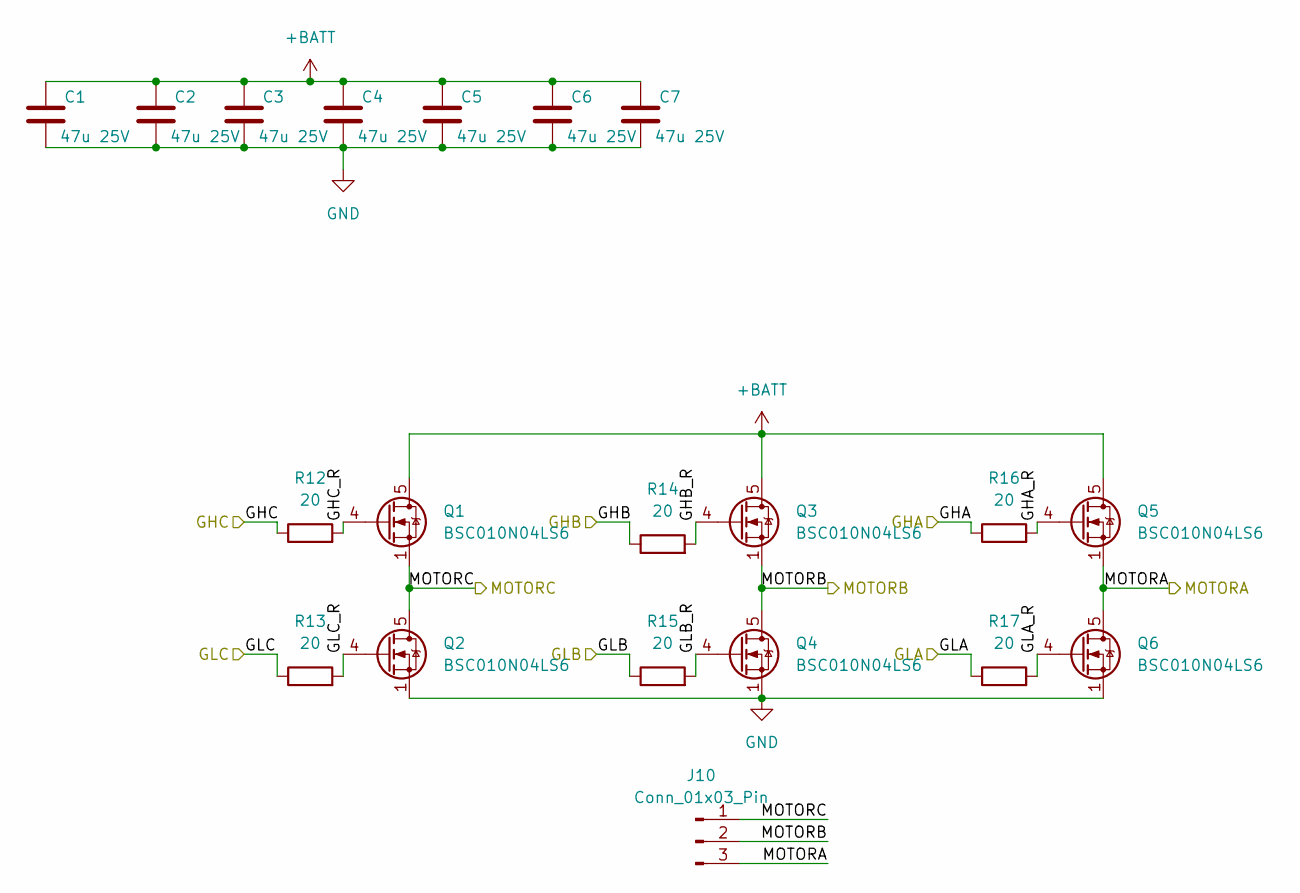
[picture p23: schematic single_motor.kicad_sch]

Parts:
C1, C2, C3, C4, C5, C6, C7: 47u 25V; C_1206_3216Metric
J10: Conn_01x03_Pin; EscMotorConnector
Q1, Q2, Q3, Q4, Q5, Q6: BSC010N04LS6; InfineonTdson8FL
R12, R13, R14, R15, R16, R17: 20; R_0402_1005Metric

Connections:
+BATT: C1.1, C2.1, C3.1, C4.1, C5.1, C6.1, C7.1, Q1.5 (D), Q3.5 (D), Q5.5 (D); also elsewhere on the board
/EscMotor1/GHA: R16.1; also elsewhere on the board
/EscMotor1/GHA_R: Q5.4 (G), R16.2
/EscMotor1/GHB: R14.1; also elsewhere on the board
/EscMotor1/GHB_R: Q3.4 (G), R14.2
/EscMotor1/GHC: R12.1; also elsewhere on the board
/EscMotor1/GHC_R: Q1.4 (G), R12.2
/EscMotor1/GLA: R17.1; also elsewhere on the board
/EscMotor1/GLA_R: Q6.4 (G), R17.2
/EscMotor1/GLB: R15.1; also elsewhere on the board
/EscMotor1/GLB_R: Q4.4 (G), R15.2
/EscMotor1/GLC: R13.1; also elsewhere on the board
/EscMotor1/GLC_R: Q2.4 (G), R13.2
/EscMotor1/MOTORA: J10.3, Q5.1 (S), Q6.5 (D); also elsewhere on the board
/EscMotor1/MOTORB: J10.2, Q3.1 (S), Q4.5 (D); also elsewhere on the board
/EscMotor1/MOTORC: J10.1, Q1.1 (S), Q2.5 (D); also elsewhere on the board
GND: C1.2, C2.2, C3.2, C4.2, C5.2, C6.2, C7.2, Q2.1 (S), Q4.1 (S), Q6.1 (S); also elsewhere on the board

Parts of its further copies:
C12, C13, C14, C15, C16, C17, C18, C19, C20, C21, C22, C23, C24, C25, C26, C27, C28, C29, C30, C31, C32: 47u 25V; C_1206_3216Metric
J4, J5, J6: Conn_01x03_Pin; EscMotorConnector
Q7, Q8, Q9, Q10, Q11, Q12, Q13, Q14, Q15, Q16, Q17, Q18, Q19, Q20, Q21, Q22, Q23, Q24: BSC010N04LS6; InfineonTdson8FL
R1, R2, R3, R4, R5, R6, R7, R8, R9, R10, R11, R18, R19, R20, R21, R22, R23, R24: 20; R_0402_1005Metric

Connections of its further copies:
+BATT: C12.1, C13.1, C14.1, C15.1, C16.1, C17.1, C18.1, C19.1, C20.1, C21.1, C22.1, C23.1, C24.1, C25.1, C26.1, C27.1, C28.1, C29.1, C30.1, C31.1, C32.1, Q7.5 (D), Q9.5 (D), Q11.5 (D), Q13.5 (D), Q15.5 (D), Q17.5 (D), Q19.5 (D), Q21.5 (D), Q23.5 (D); also elsewhere on the board
/EscMotor2/GHA: R5.1; also elsewhere on the board
/EscMotor2/GHA_R: Q11.4 (G), R5.2
/EscMotor2/GHB: R3.1; also elsewhere on the board
/EscMotor2/GHB_R: Q9.4 (G), R3.2
/EscMotor2/GHC: R1.1; also elsewhere on the board
/EscMotor2/GHC_R: Q7.4 (G), R1.2
/EscMotor2/GLA: R6.1; also elsewhere on the board
/EscMotor2/GLA_R: Q12.4 (G), R6.2
/EscMotor2/GLB: R4.1; also elsewhere on the board
/EscMotor2/GLB_R: Q10.4 (G), R4.2
/EscMotor2/GLC: R2.1; also elsewhere on the board
/EscMotor2/GLC_R: Q8.4 (G), R2.2
/EscMotor2/MOTORA: J4.3, Q11.1 (S), Q12.5 (D); also elsewhere on the board
/EscMotor2/MOTORB: J4.2, Q9.1 (S), Q10.5 (D); also elsewhere on the board
/EscMotor2/MOTORC: J4.1, Q7.1 (S), Q8.5 (D); also elsewhere on the board
/EscMotor3/GHA: R11.1; also elsewhere on the board
/EscMotor3/GHA_R: Q17.4 (G), R11.2
/EscMotor3/GHB: R9.1; also elsewhere on the board
/EscMotor3/GHB_R: Q15.4 (G), R9.2
/EscMotor3/GHC: R7.1; also elsewhere on the board
/EscMotor3/GHC_R: Q13.4 (G), R7.2
/EscMotor3/GLA: R18.1; also elsewhere on the board
/EscMotor3/GLA_R: Q18.4 (G), R18.2
/EscMotor3/GLB: R10.1; also elsewhere on the board
/EscMotor3/GLB_R: Q16.4 (G), R10.2
/EscMotor3/GLC: R8.1; also elsewhere on the board
/EscMotor3/GLC_R: Q14.4 (G), R8.2
/EscMotor3/MOTORA: J5.3, Q17.1 (S), Q18.5 (D); also elsewhere on the board
/EscMotor3/MOTORB: J5.2, Q15.1 (S), Q16.5 (D); also elsewhere on the board
/EscMotor3/MOTORC: J5.1, Q13.1 (S), Q14.5 (D); also elsewhere on the board
/EscMotor4/GHA: R23.1; also elsewhere on the board
/EscMotor4/GHA_R: Q23.4 (G), R23.2
/EscMotor4/GHB: R21.1; also elsewhere on the board
/EscMotor4/GHB_R: Q21.4 (G), R21.2
/EscMotor4/GHC: R19.1; also elsewhere on the board
/EscMotor4/GHC_R: Q19.4 (G), R19.2
/EscMotor4/GLA: R24.1; also elsewhere on the board
/EscMotor4/GLA_R: Q24.4 (G), R24.2
/EscMotor4/GLB: R22.1; also elsewhere on the board
/EscMotor4/GLB_R: Q22.4 (G), R22.2
/EscMotor4/GLC: R20.1; also elsewhere on the board
/EscMotor4/GLC_R: Q20.4 (G), R20.2
/EscMotor4/MOTORA: J6.3, Q23.1 (S), Q24.5 (D); also elsewhere on the board
/EscMotor4/MOTORB: J6.2, Q21.1 (S), Q22.5 (D); also elsewhere on the board
/EscMotor4/MOTORC: J6.1, Q19.1 (S), Q20.5 (D); also elsewhere on the board
GND: C12.2, C13.2, C14.2, C15.2, C16.2, C17.2, C18.2, C19.2, C20.2, C21.2, C22.2, C23.2, C24.2, C25.2, C26.2, C27.2, C28.2, C29.2, C30.2, C31.2, C32.2, Q8.1 (S), Q10.1 (S), Q12.1 (S), Q14.1 (S), Q16.1 (S), Q18.1 (S), Q20.1 (S), Q22.1 (S), Q24.1 (S); also elsewhere on the board

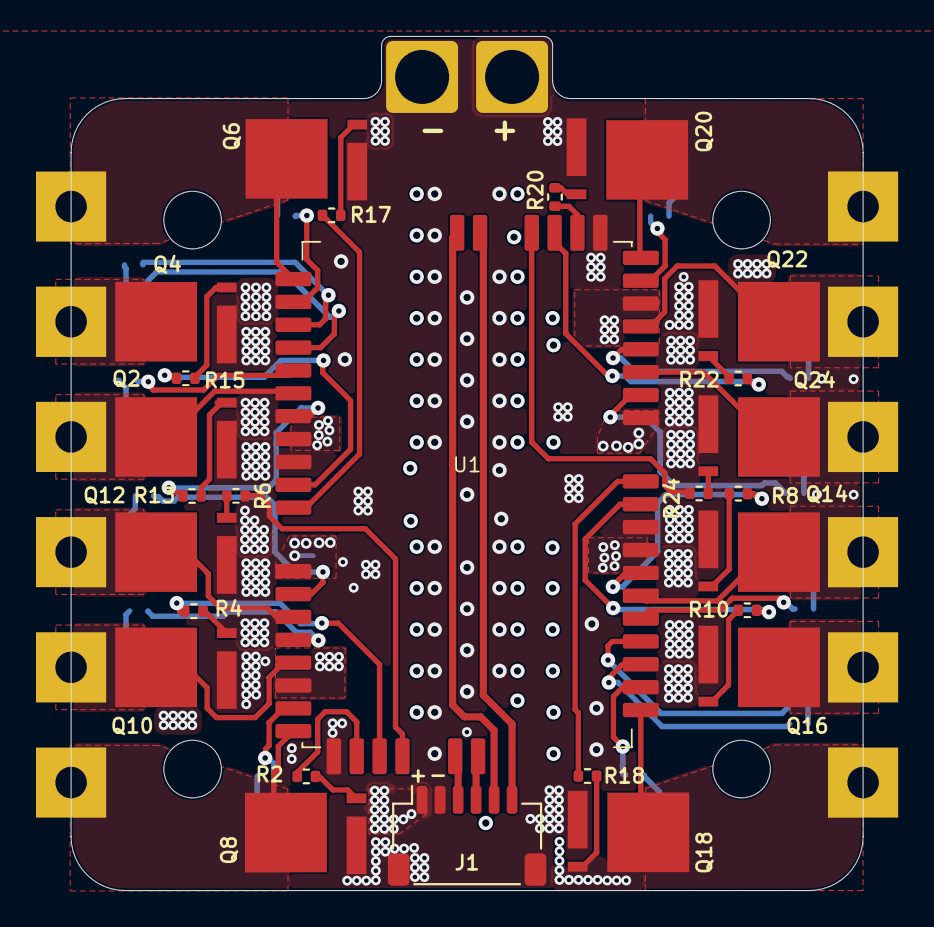
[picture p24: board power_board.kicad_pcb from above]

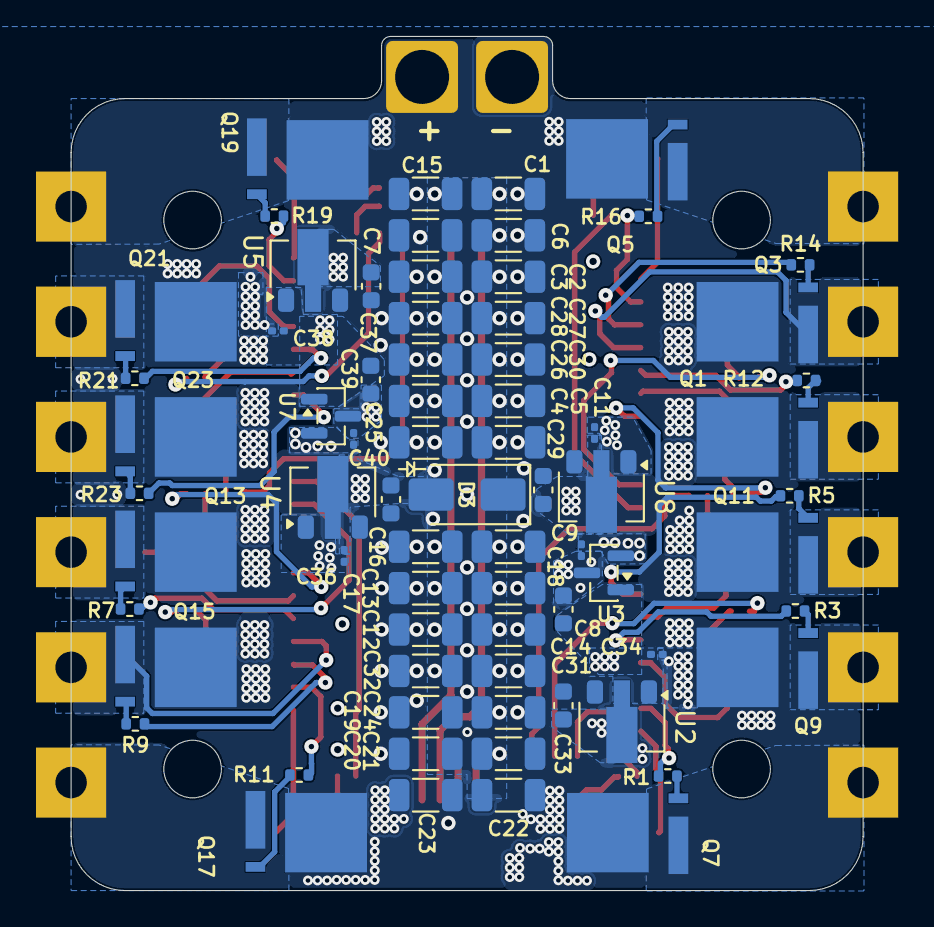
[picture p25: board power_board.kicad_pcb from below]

Board: 4 copper layers, 44.0 x 47.5 mm, 107 parts (71 on the bottom side), 72 nets.

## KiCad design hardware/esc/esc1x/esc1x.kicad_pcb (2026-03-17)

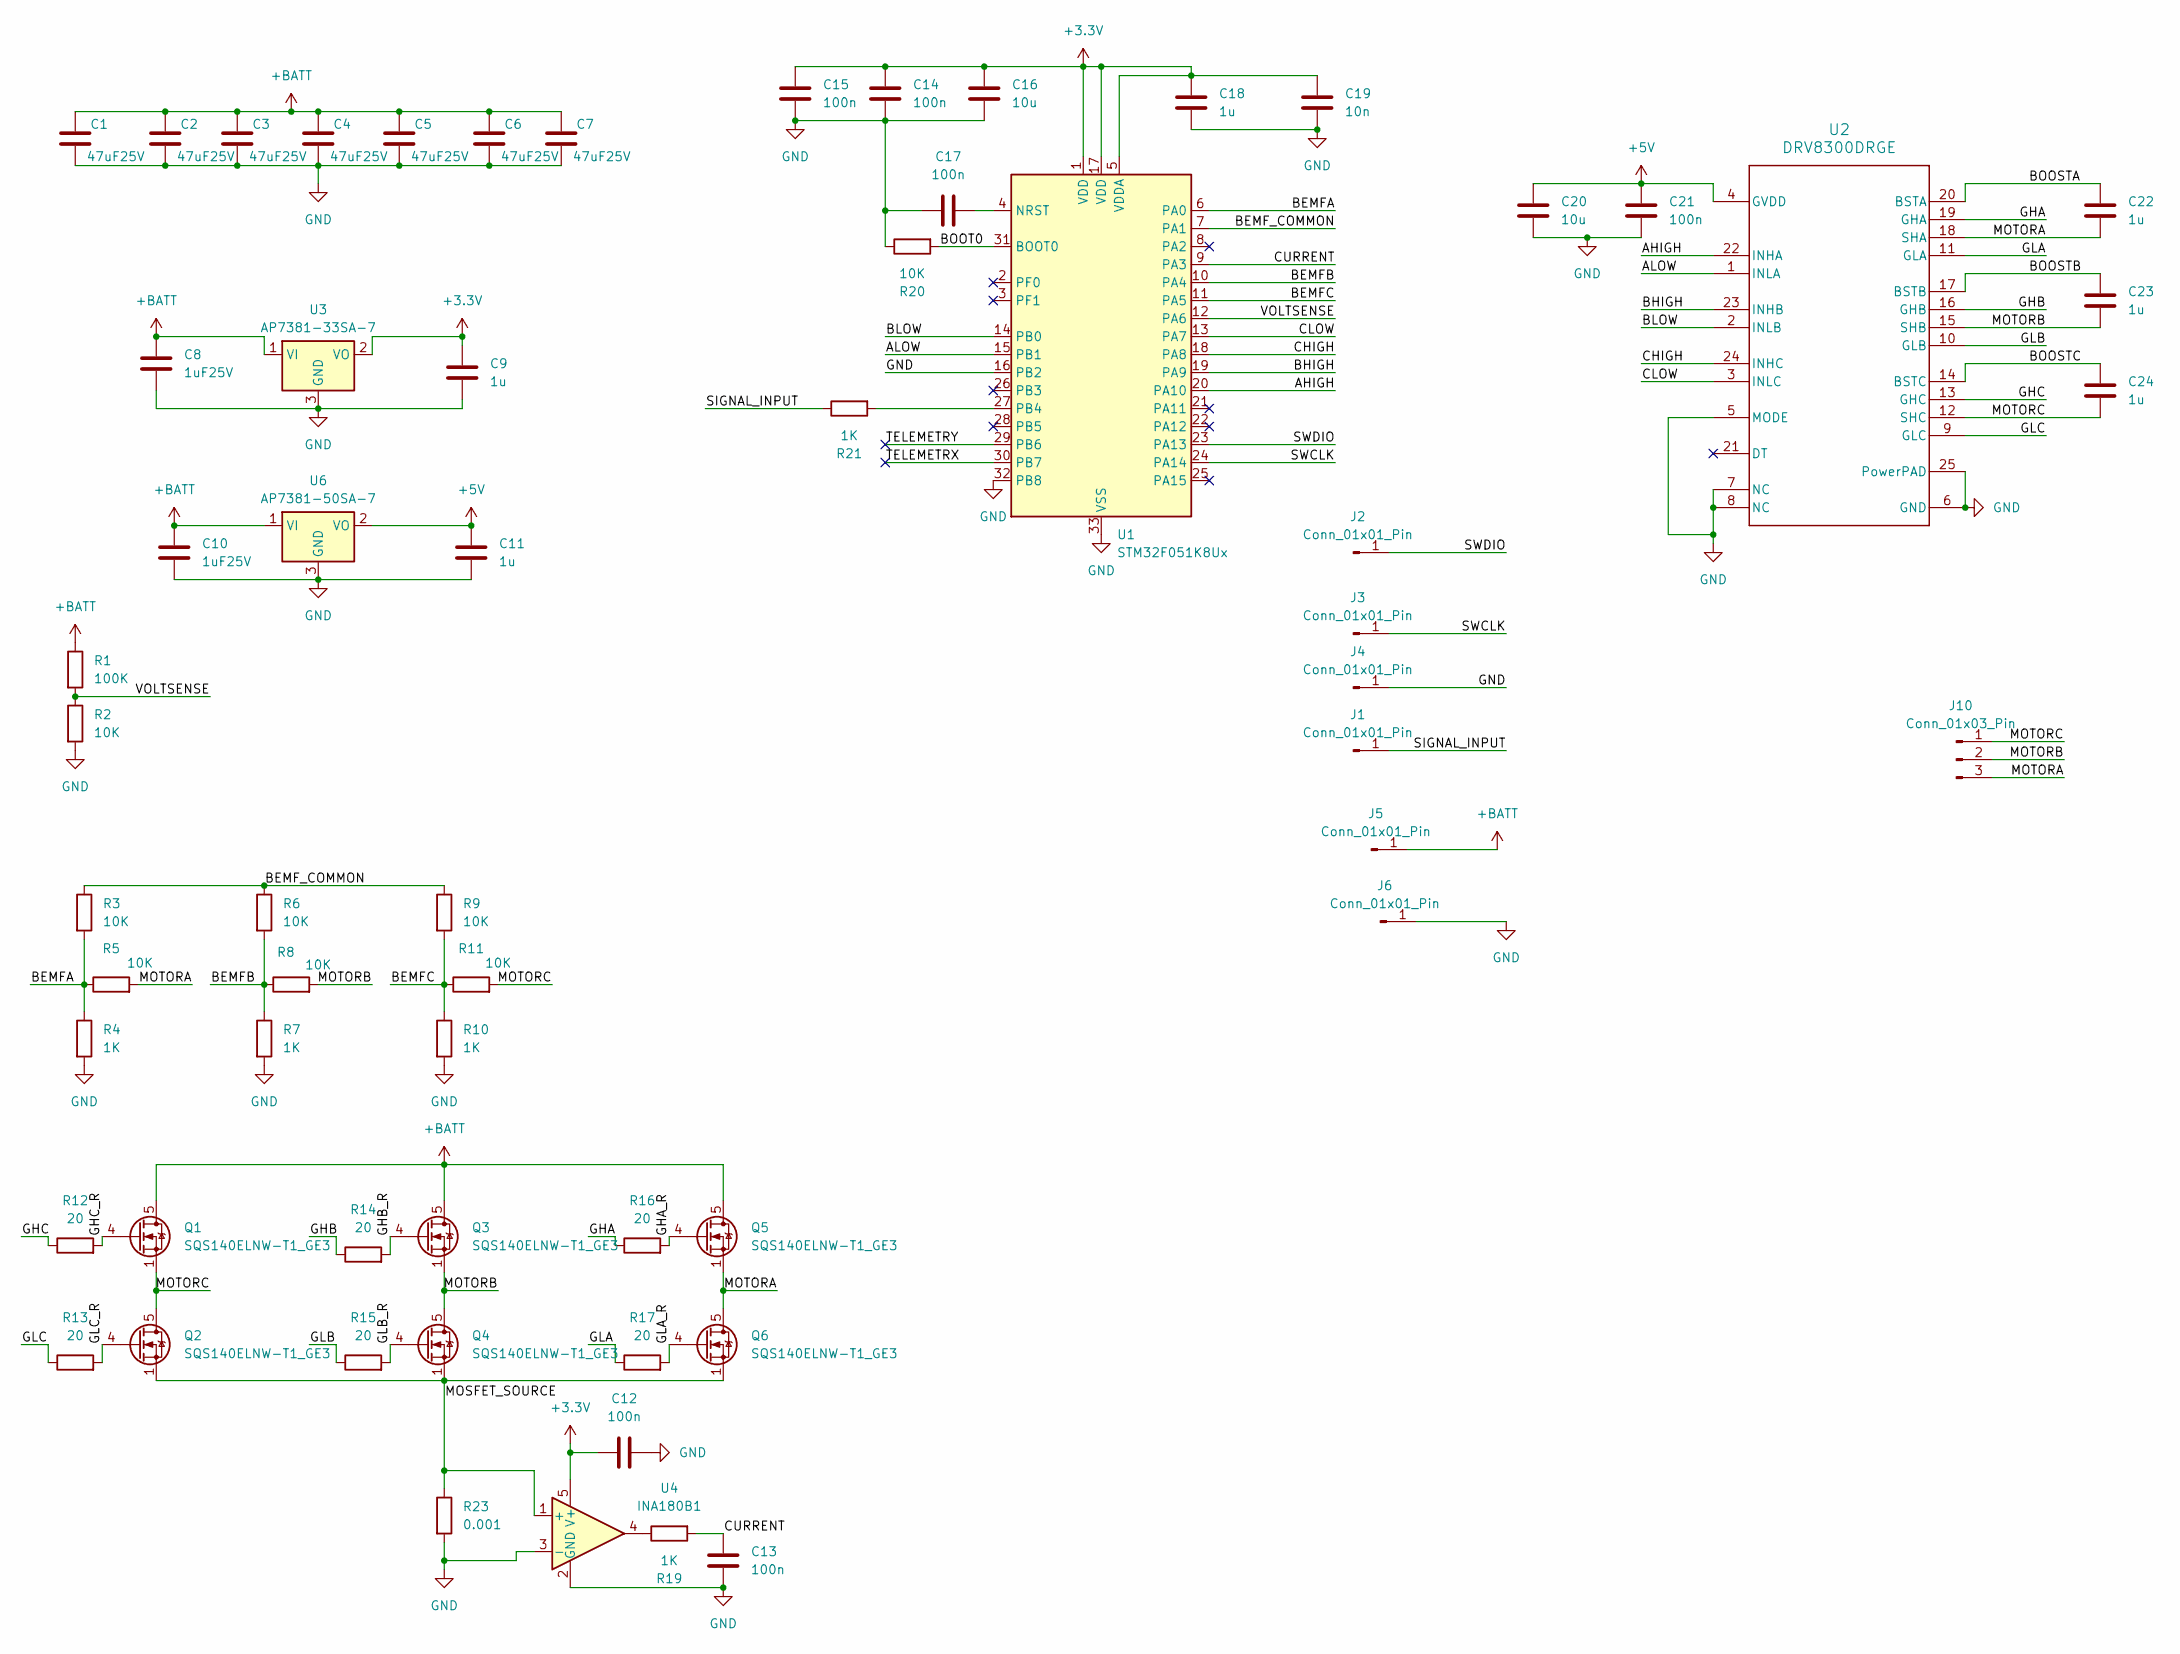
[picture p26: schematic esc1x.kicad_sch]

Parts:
C1, C2, C3, C4, C5, C6, C7: 47uF25V; C_1206_3216Metric
C8, C10: 1uF25V; C_0603_1608Metric
C9, C11, C18, C22, C23, C24: 1u; C_0201_0603Metric
C12, C13, C14, C15, C17, C21: 100n; C_0201_0603Metric
C16, C20: 10u; C_0402_1005Metric
C19: 10n; C_0201_0603Metric
J1, J2, J3, J4: Conn_01x01_Pin; SolderWirePad_1x01_SMD_1x2mm
J5, J6: Conn_01x01_Pin; EscBatteryConnector
J10: Conn_01x03_Pin; EscMotorConnector
Q1, Q2, Q3, Q4, Q5, Q6: SQS140ELNW-T1_GE3; Vishay_PowerPAK_1212-8_Single
R1: 100K; R_0402_1005Metric
R2: 10K; R_0402_1005Metric
R3, R5, R6, R8, R9, R11, R20: 10K; R_0201_0603Metric
R4, R7, R10, R19, R21: 1K; R_0201_0603Metric
R12, R13, R14, R15, R16, R17: 20; R_0402_1005Metric
R23: 0.001; R_2512_6332Metric
U1: STM32F051K8Ux; QFN-32-1EP_5x5mm_P0.5mm_EP3.45x3.45mm-Custom
U2: DRV8300DRGE; VQFN-24-1EP_4x4mm_P0.5mm_EP2.45x2.45mm_ThermalVias-Custom
U3: AP7381-33SA-7; SOT-23
U4: INA180B1; SOT-23-5
U6: AP7381-50SA-7; SOT-23

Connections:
+3.3V: C9.1, C12.1, C14.2, C15.2, C16.2, C18.1, C19.2, U1.1 (VDD), U1.5 (VDDA), U1.17 (VDD), U3.2 (VO), U4.5 (V+)
+5V: C11.1, C20.2, C21.2, U2.4 (GVDD), U6.2 (VO)
+BATT: C1.1, C2.1, C3.1, C4.1, C5.1, C6.1, C7.1, C8.1, C10.1, J5.1, Q1.5 (D), Q3.5 (D), Q5.5 (D), R1.1, U3.1 (VI), U6.1 (VI)
/AHIGH: U1.20 (PA10), U2.22 (INHA)
/ALOW: U1.15 (PB1), U2.1 (INLA)
/BEMFA: R3.2, R4.1, R5.1, U1.6 (PA0)
/BEMFB: R6.2, R7.1, R8.1, U1.10 (PA4)
/BEMFC: R9.2, R10.1, R11.1, U1.11 (PA5)
/BEMF_COMMON: R3.1, R6.1, R9.1, U1.7 (PA1)
/BHIGH: U1.19 (PA9), U2.23 (INHB)
/BLOW: U1.14 (PB0), U2.2 (INLB)
/BOOSTA: C22.2, U2.20 (BSTA)
/BOOSTB: C23.2, U2.17 (BSTB)
/BOOSTC: C24.2, U2.14 (BSTC)
/BOOT0: R20.2, U1.31 (BOOT0)
/CHIGH: U1.18 (PA8), U2.24 (INHC)
/CLOW: U1.13 (PA7), U2.3 (INLC)
/CURRENT: C13.2, R19.2, U1.9 (PA3)
/GHA: R16.1, U2.19 (GHA)
/GHA_R: Q5.4 (G), R16.2
/GHB: R14.1, U2.16 (GHB)
/GHB_R: Q3.4 (G), R14.2
/GHC: R12.1, U2.13 (GHC)
/GHC_R: Q1.4 (G), R12.2
/GLA: R17.1, U2.11 (GLA)
/GLA_R: Q6.4 (G), R17.2
/GLB: R15.1, U2.10 (GLB)
/GLB_R: Q4.4 (G), R15.2
/GLC: R13.1, U2.9 (GLC)
/GLC_R: Q2.4 (G), R13.2
/MOSFET_SOURCE: Q2.1 (S), Q2.2 (S), Q2.3 (S), Q4.1 (S), Q4.2 (S), Q4.3 (S), Q6.1 (S), Q6.2 (S), Q6.3 (S), R23.1, U4.1 (+)
/MOTORA: C22.1, J10.3, Q5.1 (S), Q5.2 (S), Q5.3 (S), Q6.5 (D), R5.2, U2.18 (SHA)
/MOTORB: C23.1, J10.2, Q3.1 (S), Q3.2 (S), Q3.3 (S), Q4.5 (D), R8.2, U2.15 (SHB)
/MOTORC: C24.1, J10.1, Q1.1 (S), Q1.2 (S), Q1.3 (S), Q2.5 (D), R11.2, U2.12 (SHC)
/SIGNAL_INPUT: J1.1, R21.1
/SWCLK: J3.1, U1.24 (PA14)
/SWDIO: J2.1, U1.23 (PA13)
/TELEMETRX: U1.30 (PB7)
/TELEMETRY: U1.29 (PB6)
/VOLTSENSE: R1.2, R2.1, U1.12 (PA6)
GND: C1.2, C2.2, C3.2, C4.2, C5.2, C6.2, C7.2, C8.2, C9.2, C10.2, C11.2, C12.2, C13.1, C14.1, C15.1, C16.1, C17.2, C18.2, C19.1, C20.1, C21.1, J4.1, J6.1, R2.2, R4.2, R7.2, R10.2, R20.1, R23.2, U1.16 (PB2), U1.32 (PB8), U1.33 (VSS), U2.5 (MODE), U2.6 (GND), U2.7 (NC), U2.8 (NC), U2.25 (PowerPAD), U3.3 (GND), U4.2 (GND), U4.3 (-), U6.3 (GND)
unnamed: R19.1, U4.4
unnamed: C17.1, U1.4 (NRST)
unnamed: R21.2, U1.27 (PB4)

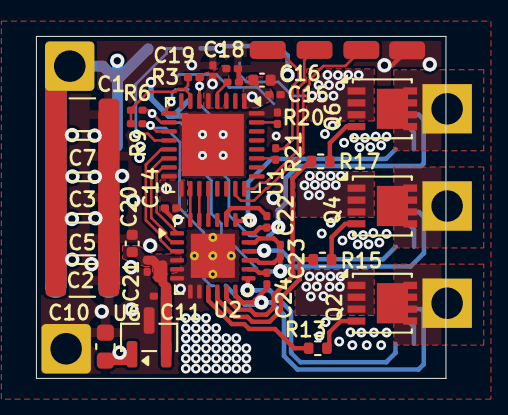
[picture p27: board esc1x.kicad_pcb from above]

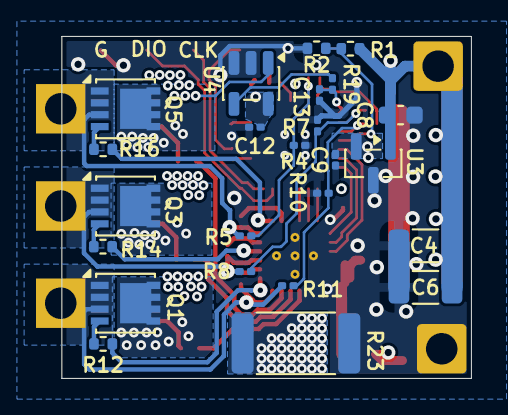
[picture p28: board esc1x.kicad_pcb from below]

Board: 4 copper layers, 22.8 x 19.0 mm, 63 parts (25 on the bottom side), 42 nets.

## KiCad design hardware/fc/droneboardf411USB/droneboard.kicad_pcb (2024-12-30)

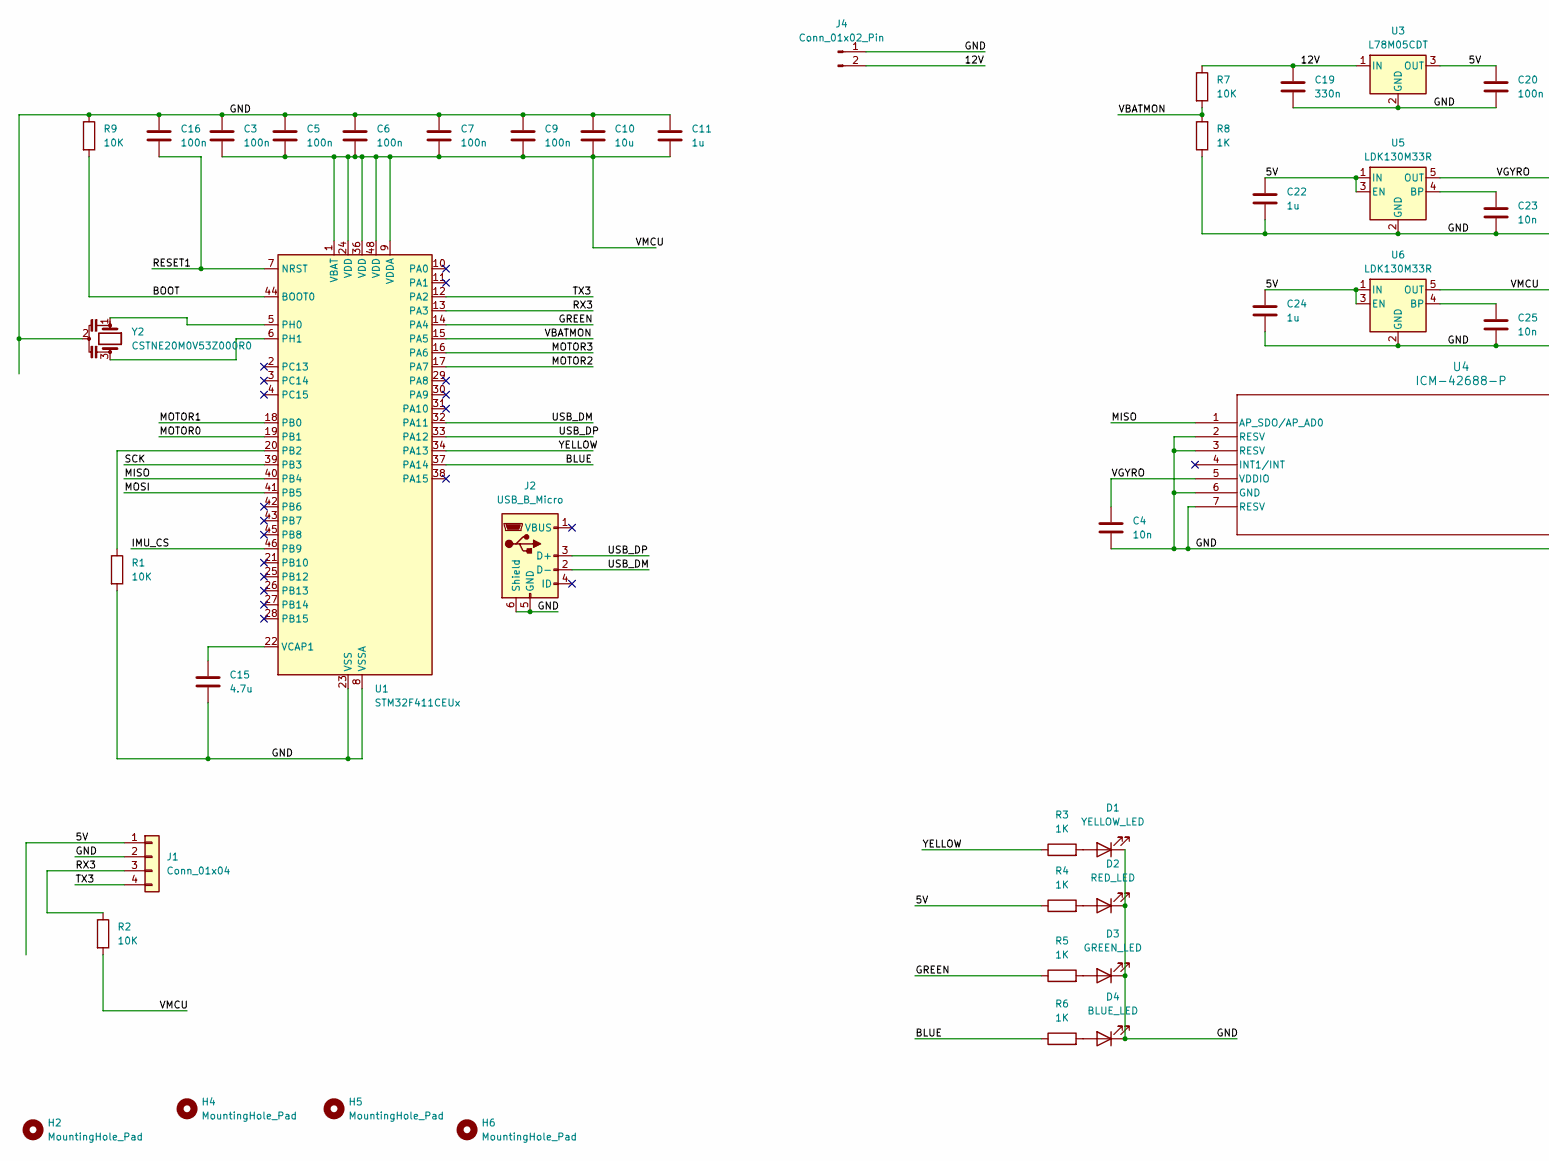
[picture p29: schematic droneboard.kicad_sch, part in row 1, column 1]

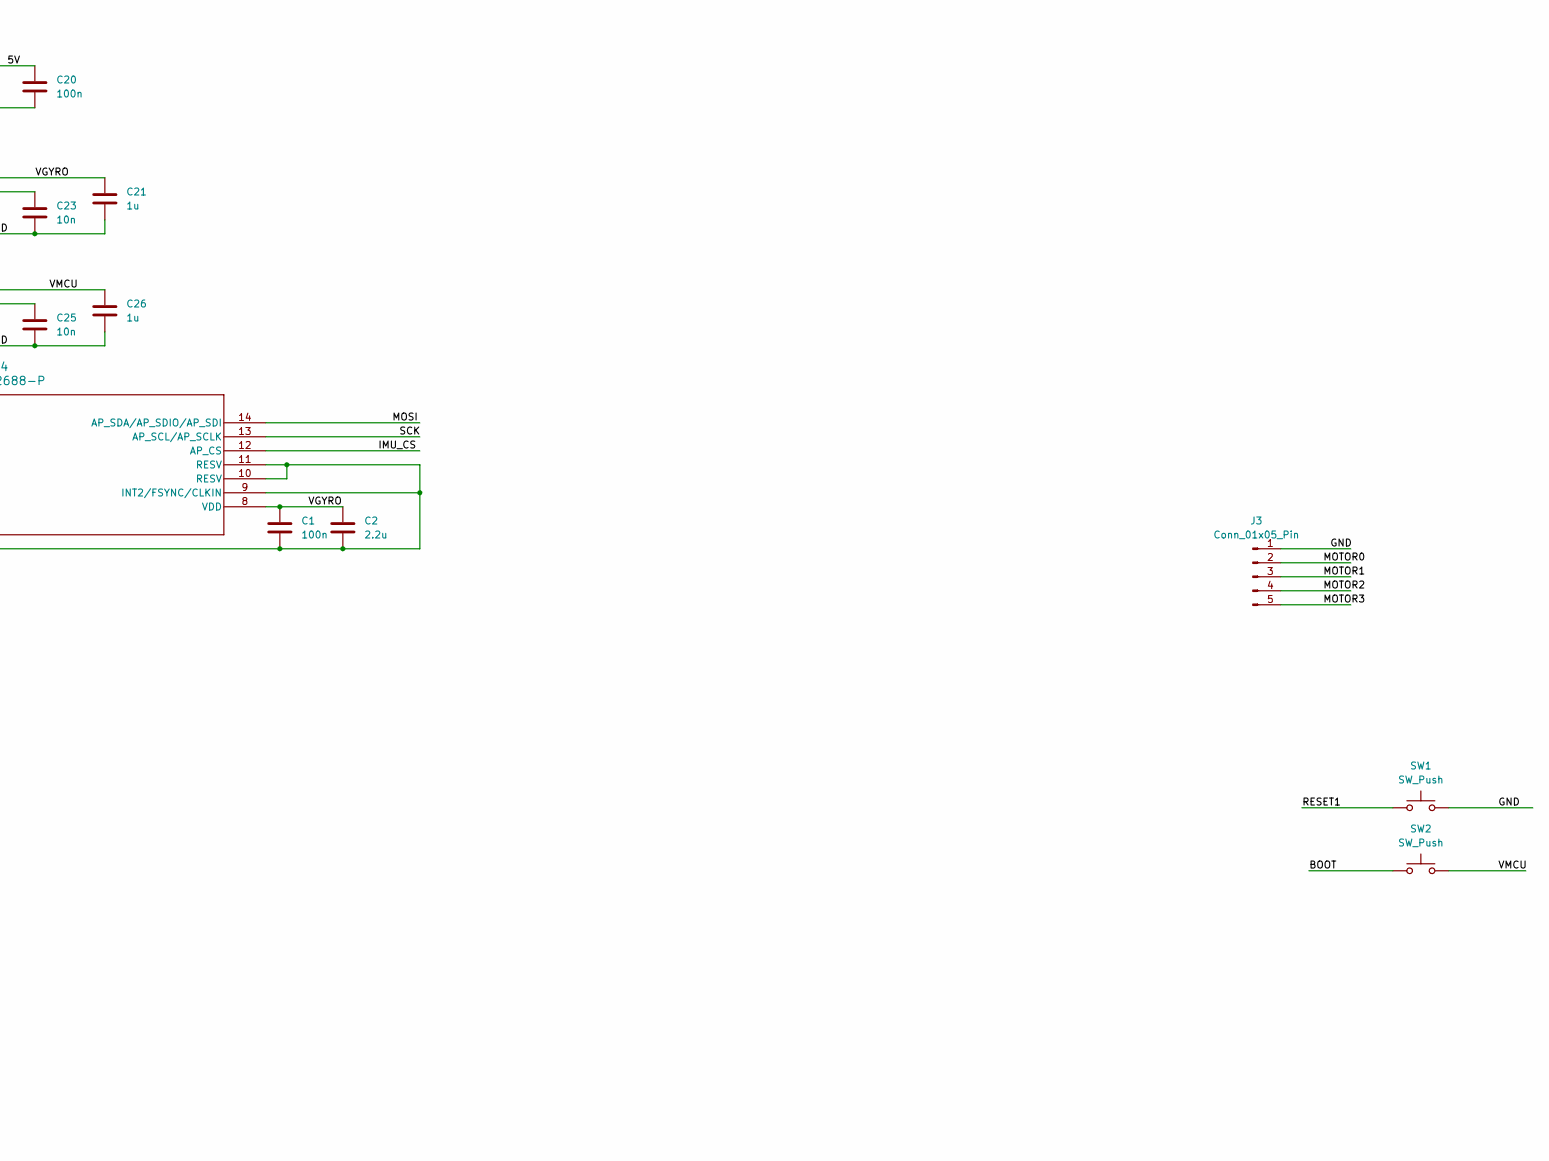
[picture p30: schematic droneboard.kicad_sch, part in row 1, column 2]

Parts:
C1, C20: 100n; C_0603_1608Metric
C2: 2.2u; C_0805_2012Metric
C3, C5, C6, C7, C9, C16: 100n; C_0402_1005Metric
C4, C23, C25: 10n; C_0603_1608Metric
C10: 10u; C_1206_3216Metric
C11, C21, C22, C24, C26: 1u; C_0805_2012Metric
C15: 4.7u; C_1206_3216Metric
C19: 330n; C_0805_2012Metric
D1: YELLOW_LED; LED_0603_1608Metric
D2: RED_LED; LED_0603_1608Metric
D3: GREEN_LED; LED_0603_1608Metric
D4: BLUE_LED; LED_0603_1608Metric
H2, H4, H5, H6: MountingHole_Pad; MountingHole_4.3mm_M4_DIN965
J1: Conn_01x04; PinHeader_1x04_P2.54mm_Vertical
J2: USB_B_Micro; USB_Micro-B_Molex_47346-0001
J3: Conn_01x05_Pin; JST_XH_B5B-XH-A_1x05_P2.50mm_Vertical
J4: Conn_01x02_Pin; JST_XH_B2B-XH-A_1x02_P2.50mm_Vertical
R1, R2, R9: 10K; R_0402_1005Metric
R3, R4, R5, R6: 1K; R_0402_1005Metric
R7: 10K; R_0603_1608Metric
R8: 1K; R_0603_1608Metric
SW1, SW2: SW_Push; SW_PUSH_1P1T_6x3.5mm_H4.3_APEM_MJTP1243
U1: STM32F411CEUx; QFN-48-1EP_7x7mm_P0.5mm_EP5.6x5.6mm
U3: L78M05CDT; TO-252-2
U4: ICM-42688-P; LGA14_2P5X3X0P91_IVS-L
U5, U6: LDK130M33R; SOT-23-5
Y2: CSTNE20M0V53Z000R0; Resonator_SMD_Murata_CSTxExxV-3Pin_3.0x1.1mm

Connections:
/5V: C20.2, C22.1, C24.1, J1.1, R4.1, U3.3 (OUT), U5.1 (IN), U5.3 (EN), U6.1 (IN), U6.3 (EN)
/12V: C19.2, J4.2, R7.1, U3.1 (IN)
/BLUE: R6.1, U1.37 (PA14)
/BOOT: R9.2, SW2.1, U1.44 (BOOT0)
/GND: C1.1, C2.2, C3.2, C4.1, C5.2, C6.2, C7.2, C9.2, C10.1, C11.1, C15.2, C16.2, C19.1, C20.1, C21.2, C22.2, C23.1, C24.2, C25.1, C26.2, D1.1 (K), D2.1 (K), D3.1 (K), D4.1 (K), J1.2, J2.5 (GND), J2.6 (Shield), J3.1, J4.1, R1.2, R8.1, R9.1, SW1.2, U1.8 (VSSA), U1.23 (VSS), U1.35 (VSS), U1.47 (VSS), U1.49 (VSS), U3.2 (GND), U4.2 (RESV), U4.3 (RESV), U4.6 (GND), U4.7 (RESV), U4.9 (INT2/FSYNC/CLKIN), U4.10 (RESV), U4.11 (RESV), U5.2 (GND), U6.2 (GND), Y2.2
/GREEN: R5.1, U1.14 (PA4)
/IMU_CS: U1.46 (PB9), U4.12 (AP_CS)
/MISO: U1.40 (PB4), U4.1 (AP_SDO/AP_AD0)
/MOSI: U1.41 (PB5), U4.14 (AP_SDA/AP_SDIO/AP_SDI)
/MOTOR0: J3.2, U1.19 (PB1)
/MOTOR1: J3.3, U1.18 (PB0)
/MOTOR2: J3.4, U1.17 (PA7)
/MOTOR3: J3.5, U1.16 (PA6)
/RESET1: C16.1, SW1.1, U1.7 (NRST)
/RX3: J1.3, R2.1, U1.13 (PA3)
/SCK: U1.39 (PB3), U4.13 (AP_SCL/AP_SCLK)
/TX3: J1.4, U1.12 (PA2)
/USB_DM: J2.2 (D-), U1.32 (PA11)
/USB_DP: J2.3 (D+), U1.33 (PA12)
/VBATMON: R7.2, R8.2, U1.15 (PA5)
/VGYRO: C1.2, C2.1, C4.2, C21.1, U4.5 (VDDIO), U4.8 (VDD), U5.5 (OUT)
/VMCU: C3.1, C5.1, C6.1, C7.1, C9.1, C10.2, C11.2, C26.1, R2.2, SW2.2, U1.1 (VBAT), U1.9 (VDDA), U1.24 (VDD), U1.36 (VDD), U1.48 (VDD), U6.5 (OUT)
/YELLOW: R3.1, U1.34 (PA13)
unnamed: D1.2 (A), R3.2
unnamed: D2.2 (A), R4.2
unnamed: D3.2 (A), R5.2
unnamed: D4.2 (A), R6.2
unnamed: R1.1, U1.20 (PB2)
unnamed: U1.5 (PH0), Y2.1
unnamed: U1.6 (PH1), Y2.3
unnamed: C15.1, U1.22 (VCAP1)
unnamed: C23.2, U5.4 (BP)
unnamed: C25.2, U6.4 (BP)


Board: 4 copper layers, 38.0 x 38.0 mm, 49 parts (0 on the bottom side), 33 nets.

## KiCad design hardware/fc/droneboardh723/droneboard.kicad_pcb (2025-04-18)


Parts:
C1, C3, C5, C6, C7, C8, C9, C16: 100n; C_0201_0603Metric
C2, C12, C15: 2.2u; C_0201_0603Metric
C4, C23, C25: 10n; C_0201_0603Metric
C10: 10u; C_0402_1005Metric
C11, C21, C22, C24, C26: 1u; C_0201_0603Metric
C13: 10u25VX7R; C_1210_3225Metric
C14: 100n25VX7R; C_0603_1608Metric
C17, C18: 22u10VX5R; C_0805_2012Metric
D1: YELLOW_LED; LED_0603_1608Metric
D2: RED_LED; LED_0603_1608Metric
D3: GREEN_LED; LED_0603_1608Metric
D4: BLUE_LED; LED_0603_1608Metric
H2, H4, H5, H6: MountingHole_Pad; MountingHole_4.3mm_M4_DIN965
J1, J2, J6: Conn_01x04; PinHeaderWide4x
J3: Conn_01x05_Pin; PinHeader_1x05_P2.00mm_Vertical
J4: Conn_01x02_Pin; PinHeader_1x02_P2.54mm_Vertical
J5: USB_C_Receptacle_USB2.0_16P; USB_C_Receptacle_GCT_USB4110
J10: Conn_01x03_Pin; PinHeader_1x03_P2.54mm_Vertical
L1: XEL4030-332MEC; L_Coilcraft_XxL4030
R1, R2, R9, R12: 10K; R_0201_0603Metric
R3, R4, R5, R6, R13: 1K; R_0402_1005Metric
R7: 10K; R_0603_1608Metric
R8: 1K; R_0603_1608Metric
R10, R11: 5.1K; R_0201_0603Metric
R14: 5.49K; R_0402_1005Metric
SW1, SW2: SW_Push; SW_PUSH_1P1T_6x3.5mm_H4.3_APEM_MJTP1243
U1: AP62300Z6; SOT-563
U2: STM32H723VGTx; LQFP-100_14x14mm_P0.5mm
U4: ICM-42688-P; LGA14_2P5X3X0P91_IVS-L
U5, U6: SPX3819M5-L-3-3; SOT-23-5
Y2: CSTNE20M0V53Z000R0; Resonator_SMD_Murata_CSTxExxV-3Pin_3.0x1.1mm

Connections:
/5V: C17.1, C18.1, C22.1, C24.1, J1.1, J2.1, J6.1, L1.2, R4.1, R14.2, U5.1 (IN), U5.3 (EN), U6.1 (IN), U6.3 (EN)
/12V: C13.1, J4.2, R7.1, U1.1 (VIN)
/BLUE: R6.1, U2.2 (PE3)
/BOOT: R9.2, SW2.1, U2.94 (BOOT0)
/GND: C1.1, C2.2, C3.2, C4.1, C5.2, C6.2, C7.2, C8.2, C9.2, C10.1, C11.1, C12.2, C13.2, C15.2, C16.2, C17.2, C18.2, C21.2, C22.2, C23.1, C24.2, C25.1, C26.2, D1.1 (K), D2.1 (K), D3.1 (K), D4.1 (K), J1.2, J2.2, J3.1, J4.1, J5.A1 (GND), J5.A12 (GND), J5.B1 (GND), J5.B12 (GND), J5.S1 (SHIELD), J6.2, J10.1, R8.1, R9.1, R10.2, R11.2, R13.1, SW1.2, U1.3 (GND), U2.10 (VSS), U2.19 (VSSA), U2.26 (VSS), U2.49 (VSS), U2.74 (VSS), U2.99 (VSS), U4.2 (RESV), U4.3 (RESV), U4.6 (GND), U4.7 (RESV), U4.9 (INT2/FSYNC/CLKIN), U4.10 (RESV), U4.11 (RESV), U5.2 (GND), U6.2 (GND), Y2.2
/GREEN: R5.1, U2.1 (PE2)
/IMU_CS: U2.93 (PB7), U4.12 (AP_CS)
/MISO: U2.90 (PB4(NJTRST)), U4.1 (AP_SDO/AP_AD0)
/MOSI: U2.91 (PB5), U4.14 (AP_SDA/AP_SDIO/AP_SDI)
/MOTOR0: J3.5, U2.42 (PE12)
/MOTOR1: J3.4, U2.43 (PE13)
/MOTOR2: J3.3, U2.44 (PE14)
/MOTOR3: J3.2, U2.45 (PE15)
/NOVBUS: J5.A4 (VBUS), J5.A9 (VBUS), J5.B4 (VBUS), J5.B9 (VBUS)
/RESET1: C16.1, SW1.1, U2.14 (NRST)
/SCK: U2.89 (PB3(JTDO), U4.13 (AP_SCL/AP_SCLK)
/SMPS_BOOST: C14.1, U1.4 (BST)
/SMPS_V: C14.2, L1.1, U1.2 (SW)
/SWCLK: J10.3, U2.76 (PA14(JTCK)
/SWDIO: J10.2, U2.72 (PA13(JTMS)
/U2RX: J1.3, R2.1, U2.25 (PA3)
/U2TX: J1.4, U2.24 (PA2)
/U4RX: J2.3, R1.1, U2.23 (PA1)
/U4TX: J2.4, U2.22 (PA0)
/U7RX: J6.3, R12.1, U2.37 (PE7)
/U7TX: J6.4, U2.38 (PE8)
/USB_DM: J5.A7 (D-), J5.B7 (D-), U2.70 (PA11)
/USB_DP: J5.A6 (D+), J5.B6 (D+), U2.71 (PA12)
/VBATMON: R7.2, R8.2, U2.28 (PA4)
/VGYRO: C1.2, C2.1, C4.2, C21.1, U4.5 (VDDIO), U4.8 (VDD), U5.5 (OUT)
/VMCU: C3.1, C5.1, C6.1, C7.1, C8.1, C9.1, C10.2, C11.2, C26.1, R1.2, R2.2, R12.2, SW2.2, U2.6 (VBAT), U2.11 (VDD), U2.20 (VREF+), U2.21 (VDDA), U2.27 (VDD), U2.50 (VDD), U2.75 (VDD), U2.100 (VDD), U6.5 (OUT)
/YELLOW: R3.1, U2.3 (PE4)
unnamed: C12.1, U2.73 (VCAP)
unnamed: C15.1, U2.48 (VCAP)
unnamed: D1.2 (A), R3.2
unnamed: D2.2 (A), R4.2
unnamed: D3.2 (A), R5.2
unnamed: D4.2 (A), R6.2
unnamed: J5.A5 (CC1), R10.1
unnamed: J5.B5 (CC2), R11.1
unnamed: R13.2, R14.1, U1.6 (FB)
unnamed: U2.12 (PH0), Y2.1
unnamed: U2.13 (PH1), Y2.3
unnamed: C23.2, U5.4 (BP)
unnamed: C25.2, U6.4 (BP)



Board: 4 copper layers, 38.0 x 38.0 mm, 62 parts (8 on the bottom side), 45 nets.

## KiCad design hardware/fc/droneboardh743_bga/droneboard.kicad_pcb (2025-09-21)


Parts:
C1, C3, C5, C6, C7, C8, C9, C16, C19, C27: 100n; C_0201_0603Metric
C2, C12, C15: 2.2u; C_0201_0603Metric
C4, C23, C25: 10n; C_0201_0603Metric
C10: 10u; C_0603_1608Metric
C11, C21, C22, C24, C26: 1u; C_0201_0603Metric
C13, C20: 10u50VX7R; C_1210_3225Metric
C14, C28: 100n50VX7R; C_0402_1005Metric
C17, C18: 22u10VX5R; C_0805_2012Metric
C29: 33n50VX5R; C_0402_1005Metric
D1: YELLOW_LED; LED_0603_1608Metric
D2: RED_LED; LED_0603_1608Metric
D3: GREEN_LED; LED_0603_1608Metric
D4: BLUE_LED; LED_0603_1608Metric
H2, H4, H5, H6: MountingHole_Pad; MountingHole_4.3mm_M4_DIN965
J1, J2: Conn_01x04_MountingPin; JST_SH_SM04B-SRSS-TB_1x04-1MP_P1.00mm_Horizontal
J3, J4: Conn_01x08_MountingPin; JST_SH_SM08B-SRSS-TB_1x08-1MP_P1.00mm_Horizontal
J5: USB_C_Receptacle_USB2.0_16P; USB_C_Receptacle_GCT_USB4110
J6, J7: Conn_01x06_MountingPin; JST_SH_SM06B-SRSS-TB_1x06-1MP_P1.00mm_Horizontal
J10: Conn_01x03_Pin; PinHeader_1x03_P2.00mm_Vertical
L1: XEL4030-332MEC; L_Coilcraft_XxL4030
Q1: DMN3042L; SOT-23
R1, R9: 10K; R_0201_0603Metric
R3, R4, R5, R6, R13: 1K; R_0402_1005Metric
R7: 10K; R_0603_1608Metric
R8: 1K; R_0603_1608Metric
R10, R11: 5.1K; R_0201_0603Metric
R14: 5.49K; R_0402_1005Metric
SW1, SW2: 434133025816; SW_Push_1P1T_NO_Vertical_Wuerth_434133025816
U1: TPS62933F; SOT-583-8
U2: STM32H743VIHx; TFBGA-100_8x8mm_Layout10x10_P0.8mm
U4: ICM-42688-P; LGA14_2P5X3X0P91_IVS-L
U5, U6: SPX3819M5-L-3-3; SOT-23-5
Y2: CSTNE8M00G520000R0; Resonator_SMD_Murata_CSTxExxV-3Pin_3.0x1.1mm

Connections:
/5V: C17.1, C18.1, C22.1, C24.1, C27.2, J1.1, J2.1, J7.1, L1.2, R4.1, R14.2, U5.1 (IN), U5.3 (EN), U6.1 (IN), U6.3 (EN)
/12V: C13.1, C20.1, C28.2, J3.1, J4.2, J6.1, R7.1, U1.3 (VIN)
/BLUE: R6.1, U2.B3 (PE3)
/BOOT: R9.2, SW2.1, U2.D5 (BOOT0)
/GND: C1.1, C2.2, C3.2, C4.1, C5.2, C6.2, C7.2, C8.2, C9.2, C10.1, C11.1, C12.2, C13.2, C15.2, C16.2, C17.2, C18.2, C19.1, C20.2, C21.2, C22.2, C23.1, C24.2, C25.1, C26.2, C27.1, C28.1, C29.1, D1.1 (K), D2.1 (K), D3.1 (K), D4.1 (K), J1.2, J1.MP (MountPin), J2.2, J2.MP (MountPin), J3.2, J3.MP (MountPin), J4.1, J4.MP (MountPin), J5.A1 (GND), J5.A12 (GND), J5.B1 (GND), J5.B12 (GND), J5.S1 (SHIELD), J6.MP (MountPin), J7.MP (MountPin), J10.1, Q1.2 (S), R1.2, R8.1, R9.1, R10.2, R11.2, R13.1, SW1.2, U1.1 (RT), U1.4 (GND), U2.A1 (PC14), U2.A2 (PC13), U2.A4 (PB9), U2.A8 (PA15), U2.B1 (PC15), U2.B4 (PB8), U2.B6 (PD5), U2.B7 (PD2), U2.B8 (PC11), U2.B9 (PC10), U2.C2 (VSS), U2.C4 (PE1), U2.C6 (PD6), U2.C7 (PD3), U2.C8 (PC12), U2.C9 (PA9), U2.D3 (PE5), U2.D4 (PE0), U2.D6 (PD7), U2.D7 (PD4), U2.D8 (PD0), U2.D9 (PA8), U2.D10 (PA10), U2.E2 (PC2_C), U2.E3 (PE6), U2.E4 (VSS), U2.E5 (VSS), U2.E6 (VSS), U2.E8 (PD1), U2.E9 (PC9), U2.E10 (PC7), U2.F1 (PC0), U2.F2 (PC1), U2.F3 (PC3_C), U2.F9 (PC8), U2.F10 (PC6), U2.G1 (VSSA), U2.G4 (PC4), U2.G5 (PB2), U2.G6 (PE10), U2.G8 (PD15), U2.G9 (PD11), U2.G10 (PB15), U2.H3 (PA5), U2.H4 (PC5), U2.H6 (PE11), U2.H8 (PD14), U2.H9 (PD10), U2.H10 (PB14), U2.J1 (VSS), U2.J3 (PA6), U2.J4 (PB0), U2.J7 (PB10), U2.J8 (PB13), U2.J9 (PD9), U2.J10 (PD13), U2.K3 (PA7), U2.K4 (PB1), U2.K7 (PB11), U2.K8 (PB12), U2.K10 (PD12), U4.2 (RESV), U4.3 (RESV), U4.6 (GND), U4.7 (RESV), U4.9 (INT2/FSYNC/CLKIN), U4.10 (RESV), U4.11 (RESV), U5.2 (GND), U6.2 (GND), Y2.2
/GREEN: R5.1, U2.A3 (PE2)
/IMU_CS: U2.A5 (PB7), U4.12 (AP_CS)
/MISO: U2.A6 (PB4), U4.1 (AP_SDO/AP_AD0)
/MOSI: U2.C5 (PB5), U4.14 (AP_SDA/AP_SDIO/AP_SDI)
/MOTOR0: J3.5, J4.5, U2.J6 (PE12)
/MOTOR1: J3.6, J4.6, U2.K6 (PE13)
/MOTOR2: J3.8, J4.4, U2.G7 (PE14)
/MOTOR3: J3.7, J4.3, U2.H7 (PE15)
/NOVBUS: J5.A4 (VBUS), J5.A9 (VBUS), J5.B4 (VBUS), J5.B9 (VBUS)
/RESET1: C16.1, SW1.1, U2.E1 (NRST)
/SCK: U2.A7 (PB3), U4.13 (AP_SCL/AP_SCLK)
/SMPS_BOOST: C14.2, U1.6 (BST)
/SMPS_V: C14.1, L1.1, U1.5 (SW)
/SWCLK: J10.3, U2.A9 (PA14)
/SWDIO: J10.2, U2.A10 (PA13)
/U2RX: J1.3, U2.K2 (PA3)
/U2TX: J1.4, U2.J2 (PA2)
/U4RX: J2.3, U2.H2 (PA1)
/U4TX: J2.4, U2.G2 (PA0)
/U7RX: J6.4, J7.4, U2.H5 (PE7)
/U7TX: J6.3, J7.3, U2.J5 (PE8)
/USB_DM: J5.A7 (D-), J5.B7 (D-), U2.C10 (PA11)
/USB_DP: J5.A6 (D+), J5.B6 (D+), U2.B10 (PA12)
/VBATMON: C19.2, R7.2, R8.2, U2.G3 (PA4)
/VFB: R13.2, R14.1, U1.8 (FB)
/VGYRO: C1.2, C2.1, C4.2, C21.1, U4.5 (VDDIO), U4.8 (VDD), U5.5 (OUT)
/VMCU: C3.1, C5.1, C6.1, C7.1, C8.1, C9.1, C10.2, C11.2, C26.1, SW2.2, U2.B2 (VBAT), U2.D2 (VDD), U2.F4 (VDDLDO), U2.F5 (VDD), U2.F6 (VDD33_USB), U2.F7 (PDR_ON), U2.H1 (VDDA), U2.K1 (VDD), U6.5 (OUT)
/VTX_GND: J6.2, J7.2, Q1.3 (D)
/VTX_PWR: Q1.1 (G), R1.1, U2.K9 (PD8)
/YELLOW: R3.1, U2.C3 (PE4)
unnamed: C12.1, U2.F8 (VCAP)
unnamed: C15.1, U2.E7 (VCAP)
unnamed: D1.2 (A), R3.2
unnamed: D2.2 (A), R4.2
unnamed: D3.2 (A), R5.2
unnamed: D4.2 (A), R6.2
unnamed: J5.A5 (CC1), R10.1
unnamed: J5.B5 (CC2), R11.1
unnamed: C29.2, U1.7 (SS)
unnamed: U2.C1 (PH0), Y2.1
unnamed: U2.D1 (PH1), Y2.3
unnamed: C23.2, U5.4 (BP)
unnamed: C25.2, U6.4 (BP)



Board: 4 copper layers, 38.0 x 38.0 mm, 67 parts (28 on the bottom side), 48 nets.

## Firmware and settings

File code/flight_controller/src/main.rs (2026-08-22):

#![no_std]
#![no_main]

use crate::{
    configurator::configurator_loop::configurator_loop, four_way::four_way_esc::FourWayParameters,
    hal::make_hardware,
};
use cortex_m_rt::entry;
use embassy_executor::SendSpawner;
use hal::get_spawners;

mod ahrs_wrapper;
mod arming;
mod battery_monitor;
mod channel_mapping;
mod crsf;
mod dshot;
mod expo_rates;
mod flight_control;

mod configurator;
mod esc;
mod four_way;
mod gps;
mod hal;
mod icm42688;
mod logging;
mod math_stuff;
mod mixer;
mod model;
mod motors;
mod msp;
mod navigation_utils;
mod osd;
mod pid;
mod shared_state;
mod static_buffer;
mod stored_config;

#[entry]
fn main() -> ! {
    let spawners = get_spawners();

    spawners
        .spawner_high
        .must_spawn(async_main(spawners.spawner_low));

    loop {
        cortex_m::asm::wfi()
    }
}

#[embassy_executor::task]
async fn async_main(spawner_low: SendSpawner) {
    let hardware = make_hardware();
    let flight_exit = flight_control::flight_main(spawner_low, hardware).await;

    match flight_exit {
        flight_control::FlightModeExit::Configurator(flight_mode_exit_data) => {
            configurator_loop(
                flight_mode_exit_data.motor_set,
                flight_mode_exit_data.shared_state,
                flight_mode_exit_data.leds,
                flight_mode_exit_data.phase,
            )
            .await;
        }
        flight_control::FlightModeExit::FourWayEsc(flight_mode_exit_data) => {
            flight_mode_exit_data
                .shared_state
                .push_four_way_mode_parameters(FourWayParameters {
                    leds: flight_mode_exit_data.leds,
                    motors: flight_mode_exit_data.motor_set.into_four_way(),
                });
        }
    }
}

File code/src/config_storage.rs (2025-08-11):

use crate::{crc8::crc8_calculate, logging::error, motors::MotorDirection};

#[cfg(feature = "flash_storage")]
use crate::hw_select::STORED_CONFIG_START;

use embassy_stm32::flash::{Blocking, Flash};
use embassy_time::Timer;
use log::info;
use zerocopy::{little_endian::F32, Immutable, IntoBytes, KnownLayout, TryFromBytes, Unaligned};

pub const STORED_CONFIG_STRUCT_SIZE: u32 = 64;

#[derive(Debug)]
pub enum StoredConfigError {
    #[allow(dead_code)]
    FlashError(embassy_stm32::flash::Error),
    FailedToDeserialize,
    ChecksumFailed,
    #[allow(dead_code)]
    ValidationError(&'static str),
}

#[derive(IntoBytes, Immutable, TryFromBytes, KnownLayout, Unaligned, Clone, Debug)]
#[repr(C)]
pub struct StoredConfig {
    pub checksum: u8,
    pub front_left_motor: u8,
    pub front_right_motor: u8,
    pub rear_left_motor: u8,
    pub rear_right_motor: u8,
    pub front_left_direction: MotorDirection,
    pub front_right_direction: MotorDirection,
    pub rear_left_direction: MotorDirection,
    pub rear_right_direction: MotorDirection,
    pub yaw_offset: F32,
    pub pitch_offset: F32,
    pub roll_offset: F32,
    pub _unused: [u8; 43],
}

impl Default for StoredConfig {
    fn default() -> Self {
        Self {
            checksum: Default::default(),
            front_left_motor: 0,
            front_right_motor: 1,
            rear_left_motor: 2,
            rear_right_motor: 3,
            front_left_direction: MotorDirection::Forward,
            front_right_direction: MotorDirection::Forward,
            rear_left_direction: MotorDirection::Forward,
            rear_right_direction: MotorDirection::Forward,
            yaw_offset: 0f32.into(),
            pitch_offset: 0f32.into(),
            roll_offset: 0f32.into(),
            _unused: [0u8; 43],
        }
    }
}

impl StoredConfig {
    fn validate(self) -> Result<Self, StoredConfigError> {
        if !self.validate_checksum() {
            Err(StoredConfigError::ChecksumFailed)
        } else if self.front_left_motor == self.front_right_motor {
            Err(StoredConfigError::ValidationError(
                "Front left and front right motors are equal",
            ))
        } else if self.front_left_motor == self.rear_left_motor {
            Err(StoredConfigError::ValidationError(
                "Front left and rear left motors are equal",
            ))
        } else if self.front_left_motor == self.rear_right_motor {
            Err(StoredConfigError::ValidationError(
                "Front left and rear right motors are equal",
            ))
        } else if self.front_right_motor == self.rear_left_motor {
            Err(StoredConfigError::ValidationError(
                "Front right and rear left motors are equal",
            ))
        } else if self.front_right_motor == self.rear_right_motor {
            Err(StoredConfigError::ValidationError(
                "Front right and rear right motors are equal",
            ))
        } else if self.rear_left_motor == self.rear_right_motor {
            Err(StoredConfigError::ValidationError(
                "Rear left and rear right motors are equal",
            ))
        } else {
            Ok(self)
        }
    }

    fn update_checksum(&mut self) {
        let bytes = self.as_bytes();
        let checksum = crc8_calculate(&bytes[1..]);

        self.checksum = checksum;
    }

    fn validate_checksum(&self) -> bool {
        let bytes = self.as_bytes();
        let checksum = crc8_calculate(&bytes[1..]);

        self.checksum == checksum
    }
}

#[allow(dead_code, clippy::field_reassign_with_default)]
#[cfg(feature = "flash_storage")]
pub async fn reconfigure_and_store(flash: &mut Flash<'static, Blocking>) {
    let mut config = StoredConfig::default();
    //let mut config = read_stored_config(flash).await;

    config.front_left_motor = 1;
    config.front_right_motor = 2;
    config.rear_left_motor = 0;
    config.rear_right_motor = 3;
    config.front_left_direction = MotorDirection::Forward;
    config.front_right_direction = MotorDirection::Backward;
    config.rear_left_direction = MotorDirection::Backward;
    config.rear_right_direction = MotorDirection::Forward;
    config.yaw_offset = (-0.11099324f32).into();
    config.pitch_offset = (0.51241034).into();
    config.roll_offset = (-0.051307525).into();

    store_config(flash, config).await;
}
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

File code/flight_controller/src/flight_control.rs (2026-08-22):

use common::configurator_protocol::messages::{FcPhase, FcStatus};
use embassy_executor::SendSpawner;
use embassy_time::{Duration, Instant, Ticker, Timer};
use static_cell::StaticCell;

use crate::{
    battery_monitor::init_battery_monitor,
    crsf::init_crsf_communication,
    esc::EscMotorSet,
    generic_hardware_type,
    gps::init_gps_receiver,
    hal::Leds,
    icm42688::ICM42688,
    logging::info,
    mixer::MotorMix,
    motors::{disarm, drive_motors, MotorInputs, MotorsContext},
    msp::usb_communication::start_usb_communication,
    osd::init_osd,
    pid::{do_pid_iteration, PidContext},
    shared_state::SharedState,
};

struct FlightContext {
    motor_context: MotorsContext,
    pid_context: PidContext,
}

pub struct FlightModeExitData {
    pub motor_set: EscMotorSet,
    pub shared_state: &'static SharedState,
    pub leds: Leds,
    pub phase: FcPhase,
}

pub enum FlightModeExit {
    Configurator(FlightModeExitData),
    FourWayEsc(FlightModeExitData),
}

pub async fn flight_main(
    spawner_low: SendSpawner,
    mut hardware: generic_hardware_type!(),
) -> FlightModeExit {
    static SHARED_STATE: StaticCell<SharedState> = StaticCell::new();

    let motor_set = hardware.motor_layout.get_motors();

    let shared_state = SHARED_STATE.init(SharedState::new(hardware.config_store));

    let mut leds: Leds = hardware.led_pins.into();

    start_usb_communication(&spawner_low, hardware.usb, shared_state).await;

    leds.green_on();

    let mut imu = ICM42688::new(hardware.imu_spi);
    let imu_result = imu.init().await;

    if imu_result.is_err() {
        return FlightModeExit::Configurator(FlightModeExitData {
            motor_set,
            shared_state,
            leds,
            phase: FcPhase::IMUInitFail,
        });
    }

    Timer::after_millis(10).await;

    leds.yellow_on();

    // stored_config::reconfigure_and_store(&mut hardware.config_store).await;
    // stored_config::dump_config(&mut hardware.config_store).await;

    let stored_config = shared_state.read_config().await;

    // icm42688::calibrate_gyro_offsets(imu, &stored_config, true).await;

    init_crsf_communication(hardware.radio_uart, &spawner_low, shared_state);
    init_battery_monitor(hardware.battery_meter, shared_state, &spawner_low);

    if let Some(gps_uart) = hardware.gps_uart {
        init_gps_receiver(gps_uart, &spawner_low, shared_state);
    }

    if let Some(msp_uart) = hardware.msp_uart {
        hardware.vtx_power_toggle.set_high();
        init_osd(
            msp_uart,
            hardware.vtx_power_toggle,
            &spawner_low,
            shared_state,
        );
    }

    leds.blue_on();

    let motor_mix: MotorMix;
    #[cfg(feature = "quad")]
    {
        use crate::mixer::QuadcopterMix;
        motor_mix = QuadcopterMix::new(motor_set, &stored_config);
    }
    #[cfg(feature = "wing")]
    {
        use crate::mixer::WingMix;

        motor_mix = WingMix::new(
            hardware.motor_layout.left_winglet_servo,
            hardware.motor_layout.right_winglet_servo,
            hardware.motor_layout.thrust_motor,
        );
    }

    let context = FlightContext {
        motor_context: MotorsContext::new(motor_mix),
        pid_context: PidContext::new(&stored_config),
    };

    flight_loop(leds, imu, context, shared_state).await
}

async fn flight_loop(
    mut leds: Leds,
    mut imu: ICM42688,
    mut context: FlightContext,
    shared_state: &'static SharedState,
) -> FlightModeExit {
    const PID_PERIOD_US: u64 = 1005;
    let mut ticker = Ticker::every(Duration::from_micros(PID_PERIOD_US));

    let mut print_counter = 0;

    leds.green_off();
    leds.blue_off();
    leds.yellow_on();

    let mut total_duration = 0f32;
    let mut inner_duration = 0f32;
    let mut previous_t1 = Instant::now();
    let mut max_measured_period = 0;
    let mut min_measured_period = 10000;

    let mut motor_inputs: MotorInputs = MotorInputs::default();

    loop {
        let t1 = Instant::now();
        let command_state = shared_state.command_snapshot();

        let armed = command_state.arming_tracker.is_armed();

        match armed {
            true => {
                leds.green_on();
                leds.yellow_off();
            }
            false => {
                leds.green_off();
                leds.yellow_on();
            }
        };

        match command_state.commands.is_fresh() {
            true => leds.blue_on(),
            false => leds.blue_off(),
        };

        if shared_state.is_four_way_mode_requested() {
            disarm(
                &mut context.motor_context,
                &motor_inputs,
                command_state.commands.beep(),
            )
            .await;

            let mix = context.motor_context.into_mix();
            let motor_set = mix.into_motors();

            return FlightModeExit::FourWayEsc(FlightModeExitData {
                motor_set,
                shared_state,
                leds,
                phase: FcPhase::Disarmed,
            });
        }

        if shared_state.is_configurator_mode_requested() {
            disarm(
                &mut context.motor_context,
                &motor_inputs,
                command_state.commands.beep(),
            )
            .await;

            let motor_set = context.motor_context.into_mix().into_motors();

            return FlightModeExit::Configurator(FlightModeExitData {
                motor_set,
                shared_state,
                leds,
                phase: FcPhase::Disarmed,
            });
        }

        print_counter += 1;
        motor_inputs =
            do_pid_iteration(&mut imu, &mut context.pid_context, &command_state.commands).await;

        let t2 = Instant::now();
        if armed {
            drive_motors(&mut context.motor_context, &motor_inputs).await;
        } else {
            disarm(
                &mut context.motor_context,
                &motor_inputs,
                command_state.commands.beep(),
            )
            .await;
        }

        let t3 = Instant::now();

        total_duration = (t3 - t1).as_micros() as f32 * 0.5 + total_duration * 0.5;
        inner_duration = (t3 - t2).as_micros() as f32 * 0.5 + inner_duration * 0.5;
        let measured_period: u64 = (t1 - previous_t1).as_micros();
        if measured_period > max_measured_period {
            max_measured_period = measured_period;
        }
        if measured_period < min_measured_period {
            min_measured_period = measured_period;
        }
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

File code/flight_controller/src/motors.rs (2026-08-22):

use core::fmt::Display;

use embassy_time::{Duration, Instant, Timer};

use crate::{esc::motor_control::BeepTone, mixer::MotorMix};

pub struct MotorsContext {
    motors: MotorMix,
    running: bool,
    beep_interval_start: Instant,
    beep_tone: BeepTone,
}

impl MotorsContext {
    pub fn new(motors: MotorMix) -> Self {
        MotorsContext {
            motors,
            running: false,
            beep_interval_start: Instant::MIN,
            beep_tone: BeepTone::Tone1,
        }
    }

    pub fn into_mix(self) -> MotorMix {
        self.motors
    }
}

pub struct MotorInputs {
    pub motor_thrust: u16,
    pub yaw_input: i16,
    pub roll_input: i16,
    pub pitch_input: i16,

    pub servo_roll: i16,
    pub servo_pitch: i16,
}

impl MotorInputs {
    pub fn idle(motor_thrust: u16, servo_roll: i16, servo_pitch: i16) -> Self {
        MotorInputs {
            motor_thrust,
            yaw_input: 0,
            roll_input: 0,
            pitch_input: 0,
            servo_roll,
            servo_pitch,
        }
    }
}

impl Default for MotorInputs {
    fn default() -> Self {
        Self::idle(0, 0, 0)
    }
}

impl Display for MotorInputs {
    fn fmt(&self, f: &mut core::fmt::Formatter<'_>) -> core::fmt::Result {
        write!(f, "sr: {}; sp: {}", self.servo_roll, self.servo_pitch)
    }
}

async fn gentle_stop(current_thrust: u16, context: &mut MotorsContext) {
    let mut thrust_target = current_thrust;

    while thrust_target > 200 {
        context.motors.same_throttle(thrust_target).await;

        Timer::after_millis(100).await;

        thrust_target = thrust_target * 70 / 100;
    }

    zero_throttle(context).await;
    context.running = false;
}

async fn zero_throttle(context: &mut MotorsContext) {
    context.motors.zero_throttle().await;
}

async fn beep_motors(context: &mut MotorsContext) {
    const BEEP_INTERVAL: Duration = Duration::from_millis(500);
    const BEEP_DUTY: Duration = Duration::from_millis(100);

    let now = Instant::now();
    let delta_t = now - context.beep_interval_start;

    if delta_t > BEEP_INTERVAL {
        context.beep_tone = context.beep_tone.next();
        context.beep_interval_start = now;
        zero_throttle(context).await;
    } else if delta_t > BEEP_DUTY {
        zero_throttle(context).await;
    } else {
        context.motors.beep_escs(context.beep_tone).await;
    }
}

pub async fn disarm(context: &mut MotorsContext, inputs: &MotorInputs, beep: bool) {
    if context.running {
        gentle_stop(
            inputs.motor_thrust / context.motors.esc_motor_couint(),
            context,
        )
        .await;
    } else if beep {
        beep_motors(context).await;
    } else {
        zero_throttle(context).await;
    }

    center_servos(context);
}

pub async fn drive_motors(context: &mut MotorsContext, inputs: &MotorInputs) {
    context.running = true;
    if inputs.motor_thrust > 0 {
        context.motors.drive_escs(inputs).await;
    } else {
        zero_throttle(context).await;
    }

    context.motors.drive_servos(inputs);
}

pub fn center_servos(context: &mut MotorsContext) {
    context.motors.center_servos();
}

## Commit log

2023-05-27 motor controll and stopping
2023-08-09 yaw PID setup, angle rollover
2023-08-11 roll/pitch pid, watchdog
2023-08-11 Wire timeout, motor watchdog
2023-08-29 BNO last
    [drone.FCStd, mpuholder.FCStd]
2023-08-31 MPU gyroonly
    [drone-PartBody.stl, drone2-DroneArm.stl, drone2.FCStd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]
2024-09-11 V3 initial
    [body.FCStd, body3.FCStd, body5.FCStd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]
2024-10-12 V3 first flight
    [body6.FCStd]
2024-10-18 filtering, battery with vref, camera mounting
    [body6.FCStd]
2024-10-24 whole model visible, faster rates, battery voltage smoothing
    [body6.FCStd]
2024-10-26 voltage round instead of trunc
    [screensholder.FCStd]
2024-11-02 motor cleanup
    [body6.FCStd, screensholder.FCStd]
2024-11-02 more cleanup
    [screensholder.FCStd]
2024-11-08 motor reset process
2024-11-09 motor refactor
2024-11-21 motor reset code
2024-12-30 USB variant
    [bom.xlsx, droneboard.kicad_pcb, droneboard.kicad_sch]
2024-12-30 Minor 3DP improvements
    [bottom.stl, frame.FCStd, legs.stl]
2025-02-03 reduce kd range, add D term low-pass filter
2025-04-18 stm32h7 board
    [bom.xlsx, droneboard.kicad_pcb, droneboard.kicad_sch]
2025-04-18 conditional compilation
    [droneboard.kicad_pcb]
2025-04-18 board work
    [droneboard.kicad_pcb, droneboard.kicad_sch]
2025-04-18 h7 hardware done
    [bom.xlsx, bottom.step, droneboard.kicad_pcb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]
2025-04-18 h7 basic work done, antenna hole on top
    [frame.FCStd, top.step]
2025-04-18 smps initial
    [droneboard.kicad_pcb, droneboard.kicad_sch]
2025-04-18 smps complete
    [IHLP2020CZ.STEP, bom.xlsx, droneboard.kicad_pcb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]
2025-04-18 smps pcb; bom
    [bom.xlsx, droneboard.kicad_pcb]
2025-04-18 SMA TOP; 20mm VTX; 3A SMPS; MSP OSD
    [droneboard.kicad_pcb, droneboard.kicad_sch, frame-PartTop.step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]
2025-04-18 battery/telemetry separation, parallel dshot, wider pin headers
    [droneboard.kicad_pcb, droneboard.kicad_sch]
2025-04-18 h723 further work
    [bom.xlsx, droneboard.kicad_pcb, droneboard.kicad_sch]
2025-04-18 kicad update
    [droneboard.kicad_pcb]
2025-04-27 recalibrate gyro for h7
2025-05-12 prioritize PID loop task; enable cache on h7
2025-05-20 fixed d-term; throttle limit on potentiometer
    [channel_mapping.rs, main.rs, pid.rs]
2025-05-26 angle mode; align gyro to controls
2025-06-27 UBX gps receive, show gps on msp, send gps over telemetry
    [frame.FCStd, top.step, top.stl]
2025-07-04 better gps mount, number2string fixes
    [frame.FCStd]
2025-07-05 fix ordering of lat/lon in nav-pvt ubx packet
    [gps.rs]
2025-07-19 gps mount on frame, frame stls cleanup
    [bottom.step, bottom.stl, complete.step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]
2025-08-11 H743 bga drone board Hardware: - switchable VTX power - BGA MCU - 6S support
    Code:
    - refactor calibration logic
    [434133025816.stp, IHLP2020CZ.STEP, KMR221GLFS--3DModel-STEP-56544.STEP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]
2025-08-15 hardware selection refactoring
    [lr-frame.FCStd]
2025-09-21 HAL fixes, remove 5V diode
    [droneboard.kicad_pcb, droneboard.kicad_sch]
2025-10-03 add 7 inch frame
    [arm.step, arm.stl, bottom.step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]
2025-10-05 Arm tolerance fixes
    [arm.step, seven_inch.FCStd]
2025-10-18 seven inch PID values update
2025-10-28 7inch gps plate, whole assembly
    [gps_plate.step, gps_plate.stl, seven_inch.FCStd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]
2026-01-21 five inch leg fix
    [legs.step, legs.stl]
2026-01-21 five inch leg fix part 2
    [five_inch.FCStd]
2026-03-17 support for servos and wing layout
2026-03-17 esc initial attempt
    [bom.xlsx, esc.kicad_pcb, esc.kicad_sch]
2026-03-17 Implement 1x esc. Reorganize hardware folder
    [434133025816.stp, IHLP2020CZ.STEP, KMR221GLFS--3DModel-STEP-56544.STEP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]
2026-03-18 angle mode yaw fix, pre-arm logic
    [channel_mapping.rs, main.rs, pid.rs]
2026-04-26 stored config error log improvements
    [main.rs]
2026-04-26 4X ESC
    [PG_TDSON_FL.stp, SM06B-SRSS-TB--3DModel-STEP-269445.STEP, bom.xlsx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]
2026-04-26 Wider ESC battery holes
    [power_board.kicad_pcb]
2026-04-29 ESC readme
2026-05-10 Ignore KiCad history folders
2026-05-25 thermal vias fix
    [logic_board.kicad_pcb]
